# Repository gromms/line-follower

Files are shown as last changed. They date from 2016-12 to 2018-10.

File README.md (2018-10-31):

# line-follower

## Team

* Gromet Spaal
* Juhan Raedov

## Description

Goal is to develop a line follower robot that would be able to compete and
complete the track of Robotex line following with obstacles and regular line
following. The emphasis will be on line following with obstacles. 

The design will be based on [Jarek Korus'es Thunderstorm] (https://www.youtube.com/watch?v=a7_z5ovXjRw)

## Main Requirements

* Max Dimensions:  25x25x25 cm
* Max Weight: 1 kg
* Must have a start/stop button or remote
* Voltage up to 24 V

## Features

* Remote which can be used to:
 * Start and stop the line following program
 * Monitor battery voltage
 * Change PID constants
 * Control blower (on-off, speed)
 * Choose whether to use normal line following or line following with obstacles
* Sensors:
 * 14 IR light sensors for line detection
 * 2-axis accelerometer to calculate tilt angles
 * Three IR proximity sensors to detect the obstacles
 * Li-Po monitoring IC
* Arduino mini for live WiFi or bluetooth feedback of sensors (maybe include it onto main board)
 * **Reasoning:**
  - Reduces time when the main processor has to deal with things that are not related to running the main program
  - Deals with the communication with the remote
  - Can give live feedback of the sensors
   - Can be used to save the data and plot a graph of line errors

## BOM
[Google Drive spreadsheet] (https://docs.google.com/spreadsheets/d/14ZZVYrouCOKjxGVaX2KsAmJzS4HpelGW_TXLZ0HPqsI/edit#gid=0)

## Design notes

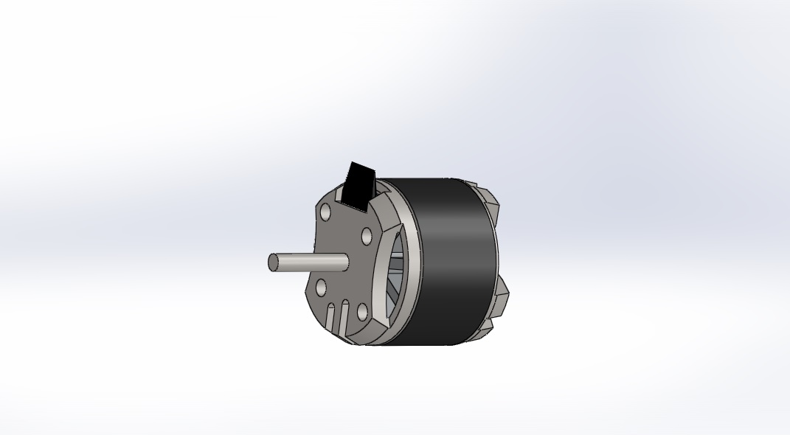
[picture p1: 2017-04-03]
SW design/Martini sumo rattad/PropDrive 28-26/Render2.jpg

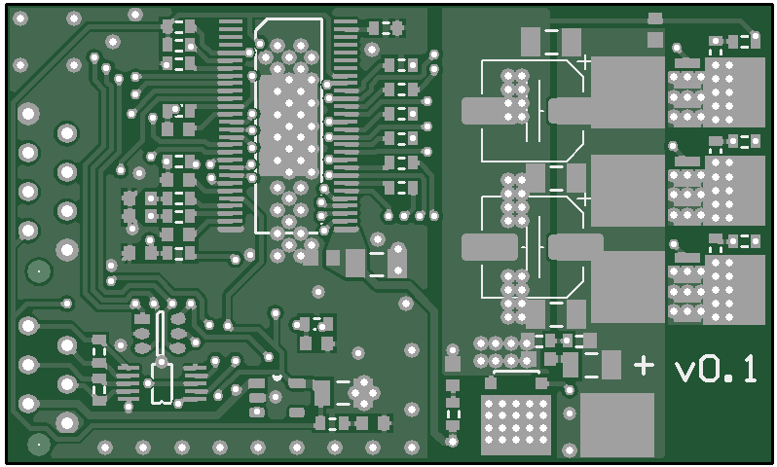
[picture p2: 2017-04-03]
SW design/bldc_driver/ibd_v01_top.png

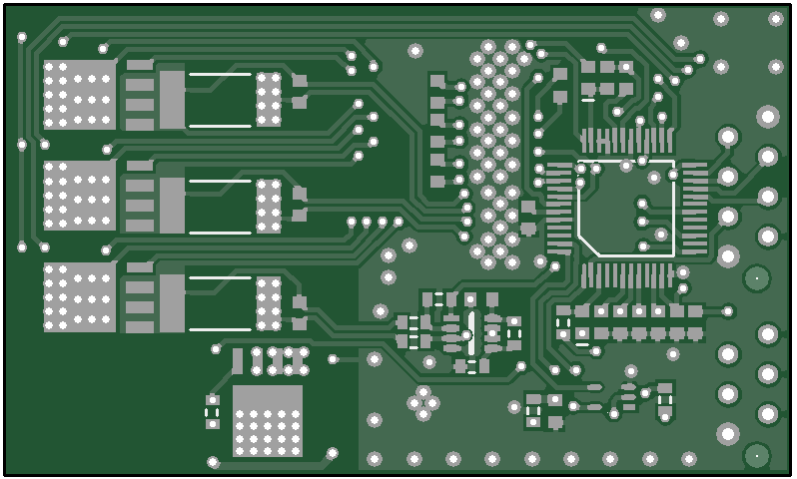
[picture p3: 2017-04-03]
SW design/bldc_driver/ibd_v01_bottom.png

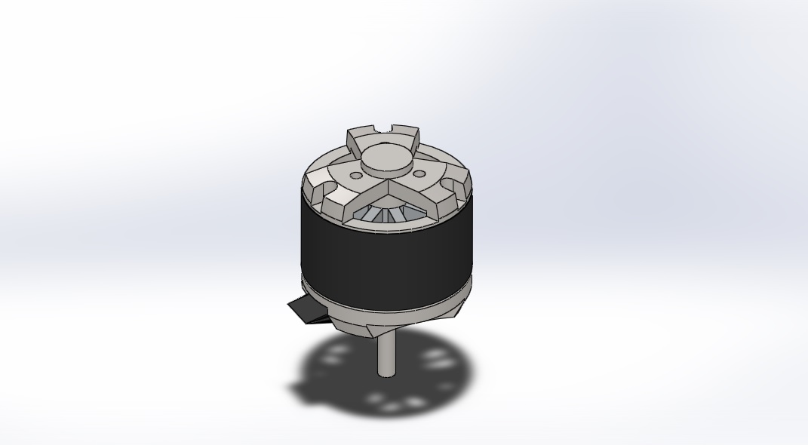
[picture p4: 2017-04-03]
SW design/Martini sumo rattad/PropDrive 28-26/Render1.jpg

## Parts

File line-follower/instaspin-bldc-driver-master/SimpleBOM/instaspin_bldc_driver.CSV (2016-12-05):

Bill of Material for
On 14.08.2016 at 22:21:20
Comment | Pattern | Quantity | Components
1.00k | J1-0603 | 2 | R32, R33 | Resistor
10.0k | J1-0603 | 3 | R34, R36, R37 | Resistor
100k | J1-0603 | 1 | R17 | Resistor
100nF | 1608[0603] | 12 | C10, C11, C12, C15, C16, C17, C18, C20, C22, C31, C32, C34 | Capacitor (Semiconductor SIM Model)
10k | J1-0603 | 4 | R26, R27, R35, R38 | Resistor
10m | 2512M | 3 | R7, R8, R9 | Resistor
10nF | 1608[0603] | 1 | C21 | Capacitor (Semiconductor SIM Model)
10R | J1-0603 | 6 | R1, R2, R3, R4, R5, R6 | Resistor
10uF | C1206 | 1 | C37 | Capacitor (Semiconductor SIM Model)
120R | J1-0603 | 2 | R44, R47 | Resistor
1k | J1-0603 | 2 | R10, R25 | Resistor
1nF | 1608[0603] | 3 | C7, C8, C9 | Capacitor (Semiconductor SIM Model)
1R | J1-0603 | 1 | R28 | Resistor
1uF | 1608[0603] | 2 | C1, C2 | Capacitor (Semiconductor SIM Model)
2.2k | J1-0603 | 2 | R24, R48 | Resistor
2.2nF | 1608[0603] | 3 | C23, C24, C25 | Capacitor (Semiconductor SIM Model)
2.2uF | 1608[0603] | 7 | C3, C26, C27, C28, C29, C30, C35 | Capacitor (Semiconductor SIM Model)
2.2uF | C1206 | 4 | C4, C5, C6, C14 | Capacitor (Semiconductor SIM Model)
220 OHM | INDC1608L | 1 | FB1 | Ferrite
220µ | CAP_ELEC_6.3x4.2 | 2 | C39, C40 | Capacitor THT Alum Elec 470uF 20% 16V
22nF | 1608[0603] | 1 | C13 | Capacitor (Semiconductor SIM Model)
25AA010 | TSOT-23-6 | 1 | U8 | EEPROM
3.3R | C1206 | 1 | R18 | Resistor
330R | J1-0603 | 1 | R42 | Resistor
34.8k | J1-0603 | 4 | R11, R12, R13, R19 | Resistor
4.7k | J1-0603 | 1 | R41 | Resistor
4.99k | J1-0603 | 4 | R14, R15, R16, R20 | Resistor
56R | J1-0603 | 3 | R21, R22, R23 | Resistor
60 OHM | INDC1608L | 1 | FB2 | Ferrite
DRV8301 | SO56_POWERPAD | 1 | U2
HEADER-1 | 2MM-BANANA-SOCKET | 5 | J16, J17, J18, J19, J26
JTAG | MICRO-MATCH-8 | 1 | J12
LED1 | 1608[0603] | 2 | D2, D3 | Typical RED GaAs LED
MOSFET-N | SOT669 | 7 | Q1, Q2, Q3, Q4, Q5, Q6, Q7
NUP4201MR6 | TSOP-6 | 1 | U3
OPA2374 | SOT23-8 | 1 | U4
RS485 | MICRO-MATCH-6 | 1 | J13
SN65HVD73 | SOP10 | 1 | U6
ZENER | SODFL370X135-2N | 1 | D1
TMS320F28027F | PQFP48 | 1 | U1

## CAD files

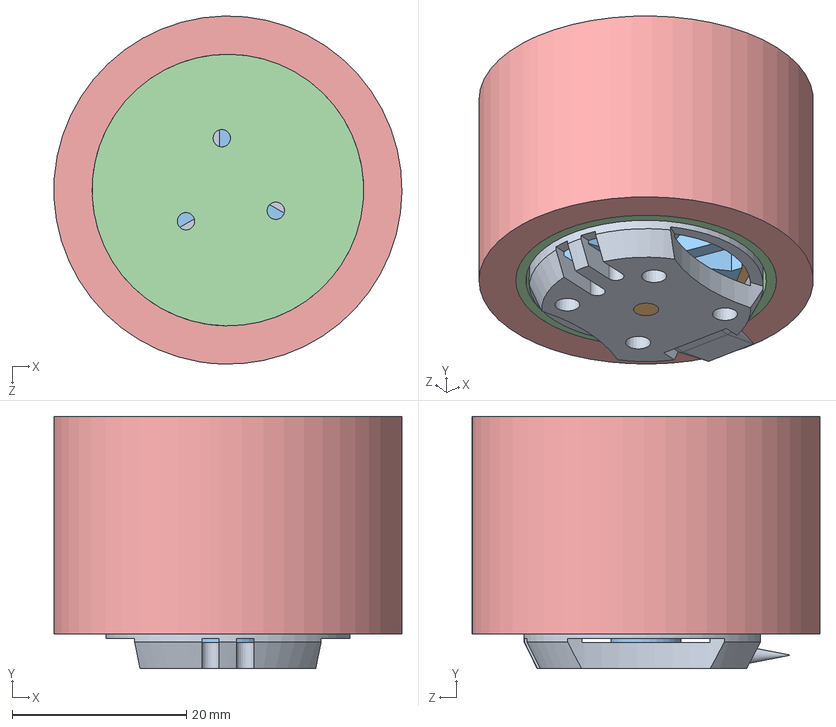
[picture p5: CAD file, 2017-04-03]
SW design/Martini sumo rattad/rehvi_raam_ja_mootor.SLDASM
40.0 x 29.0 x 40.0 mm
StatMotore
CassaMotore
InternoMotore
rehvi_raam
rehv

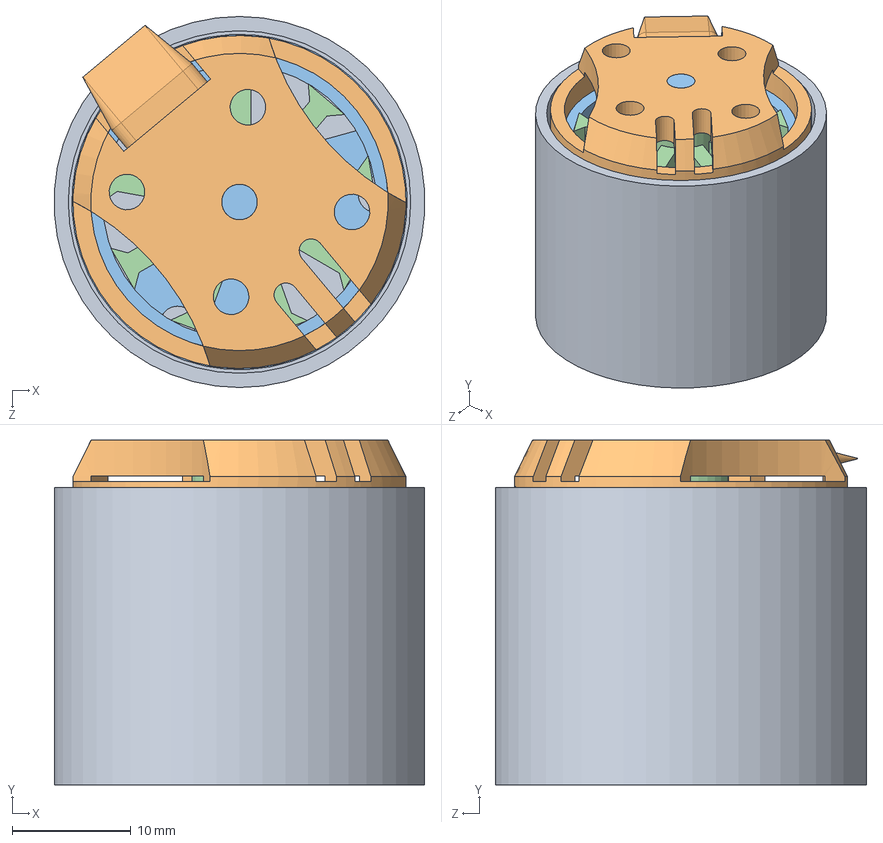
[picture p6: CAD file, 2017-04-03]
SW design/Martini sumo rattad/mootor_raamis.SLDASM
31.1 x 29.0 x 31.2 mm
rehvi_raam
StatMotore
CassaMotore
InternoMotore

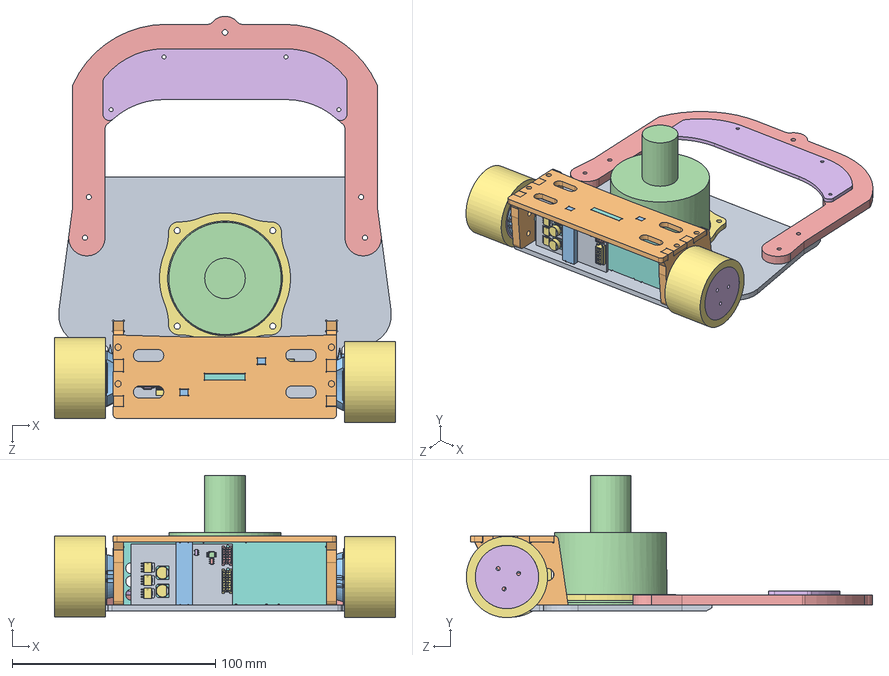
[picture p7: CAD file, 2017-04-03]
SW design/MAIN.SLDASM
167.8 x 70.0 x 199.9 mm
base
motor_mnt x 2
StatMotore x 2
CassaMotore x 2
InternoMotore x 2
rehvi_raam x 2
rehv x 2
motor_mnt_support
ibd01_Board x 2
ibd01_User_Library-sot238 x 2
ibd01_User_Library-sot353 x 2
ibd01_User_Library-msop-10 x 2
ibd01_micromatch_body_Pins6 x 2
ibd01_micromatch_pin x 12
ibd01_micromatch_body_Pins8 x 2
ibd01_micromatch_pin_2 x 16
ibd01_User_Library-LFPAK_1_1 x 14
ibd01_User_Library-LFPAK_2_1 x 14
ibd01_User_Library-LFPAK_3_1 x 14
ibd01_User_Library-LFPAK_4_1 x 14
ibd01_User_Library-LFPAK_5_1 x 14
ibd01_User_Library-LFPAK_6_1 x 14
ibd01_User_Library-LFPAK_7_1 x 14
ibd01_User_Library-LQFP48-2_case x 2
ibd01_User_Library-LQFP48-2_pin x 96
ibd01_User_Library-LQFP48-2_circle x 2
ibd01_Extruded_6 x 12
ibd01_Extruded_7 x 6
ibd01_User_Library-TSOP-6 x 2
ibd01_CircuitWorks-SOT-23-5 x 2
ibd01_Cap,_elec,_6.3x4.2 x 4
ibd01_Cap,_elec,_6.3x4.2_2 x 4
ibd01_Cap,_elec,_6.3x4.2_3 x 4
roof
ibd01_fastener x 2
edf
front5mm
front_sensors
edf_mnt

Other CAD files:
SW design/bldc_driver/ibd01_779537936.sldasm
SW design/bldc_driver/ibd01_Q6.sldasm
SW design/bldc_driver/ibd01_R8.sldasm
SW design/bldc_driver/ibd01_U3.sldasm
SW design/bldc_driver/ibd01_U4.sldasm
SW design/bldc_driver/ibd01_Q4.sldasm
SW design/bldc_driver/ibd01_U5.sldasm
SW design/bldc_driver/ibd01_R7.sldasm
SW design/bldc_driver/ibd01_J12.sldasm
SW design/bldc_driver/ibd01_micromatch_fob_6.sldasm
SW design/bldc_driver/ibd01_U1.sldasm
SW design/bldc_driver/ibd01_U7.sldasm
SW design/bldc_driver/ibd01_Q3.sldasm
SW design/bldc_driver/ibd01_C40.sldasm
SW design/bldc_driver/ibd01_User_Library-LFPAK.sldasm
SW design/2/anduriplaat.SLDPRT
SW design/2/base.SLDPRT
SW design/2/front.SLDPRT
SW design/Martini sumo rattad/PropDrive 28-26/CassaMotore.SLDPRT
SW design/Martini sumo rattad/PropDrive 28-26/InternoMotore.SLDPRT
SW design/Martini sumo rattad/PropDrive 28-26/PropDrive28-26.IGS
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

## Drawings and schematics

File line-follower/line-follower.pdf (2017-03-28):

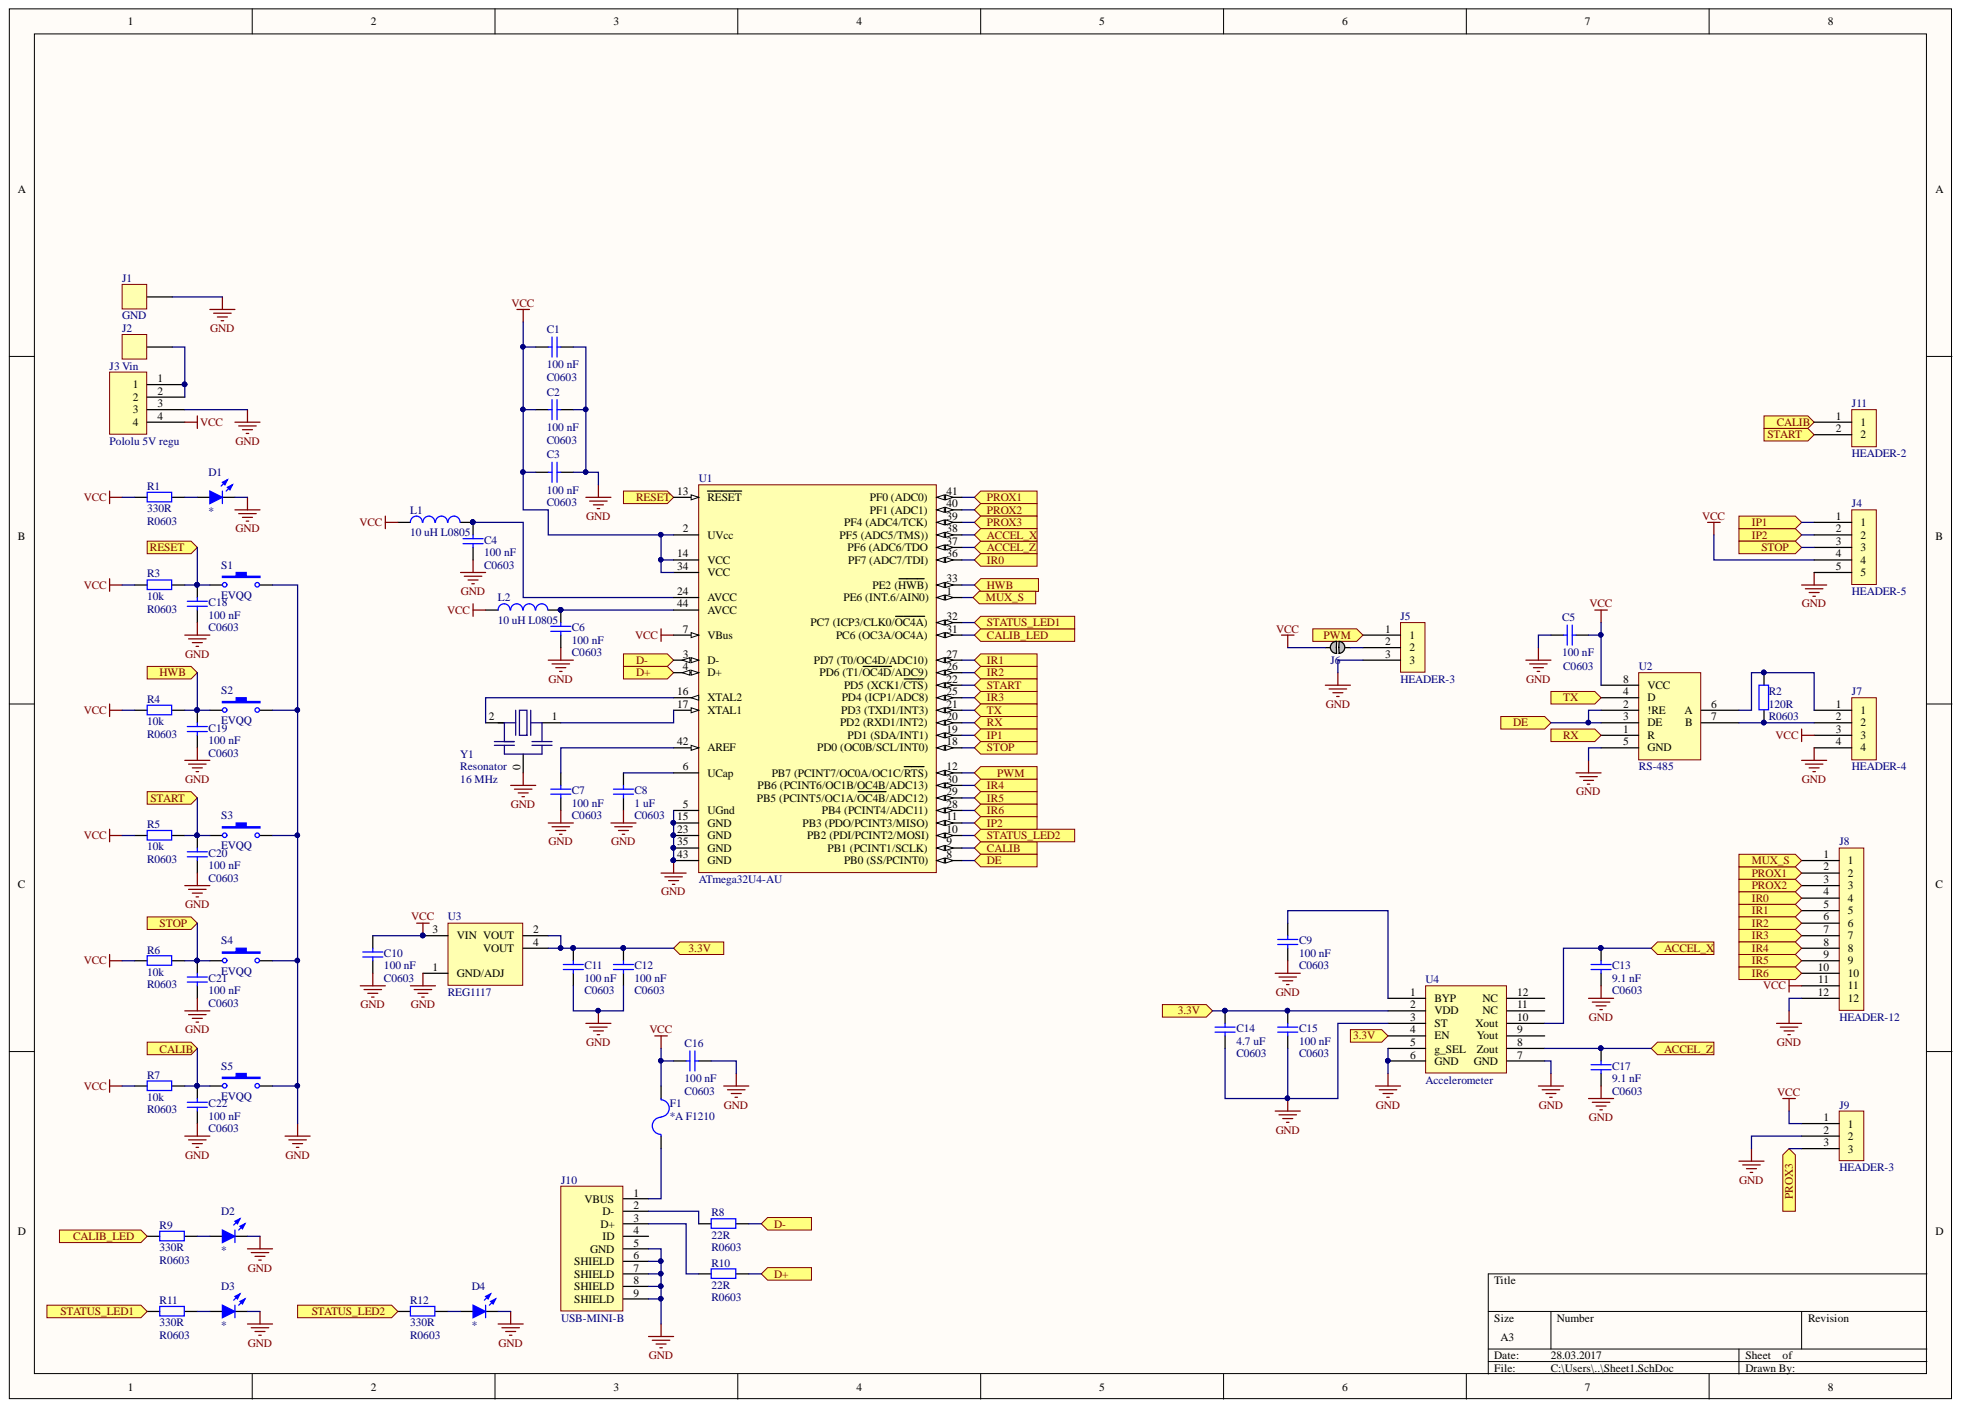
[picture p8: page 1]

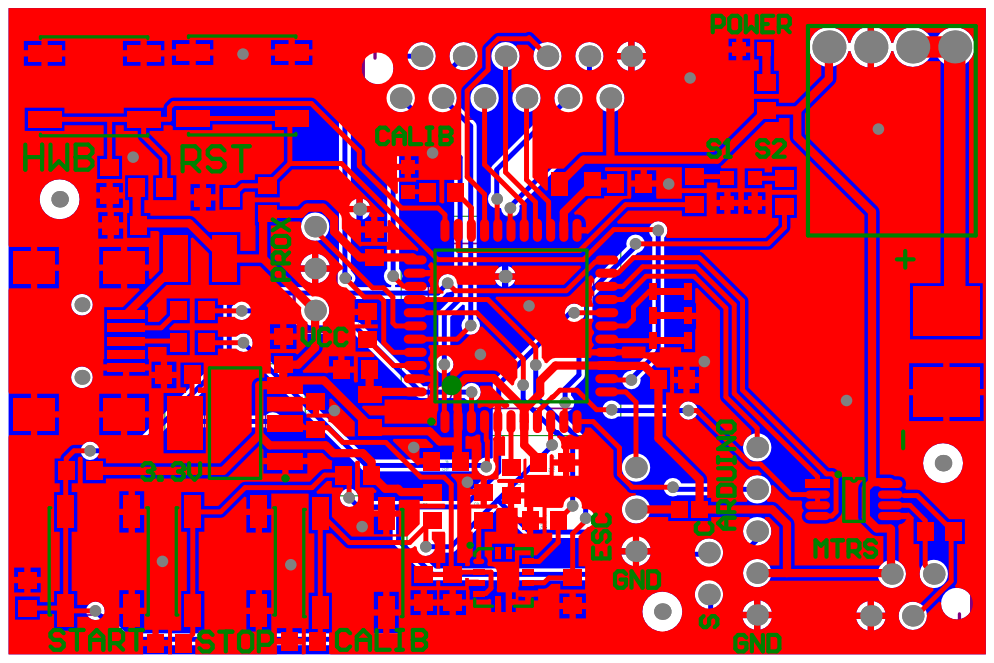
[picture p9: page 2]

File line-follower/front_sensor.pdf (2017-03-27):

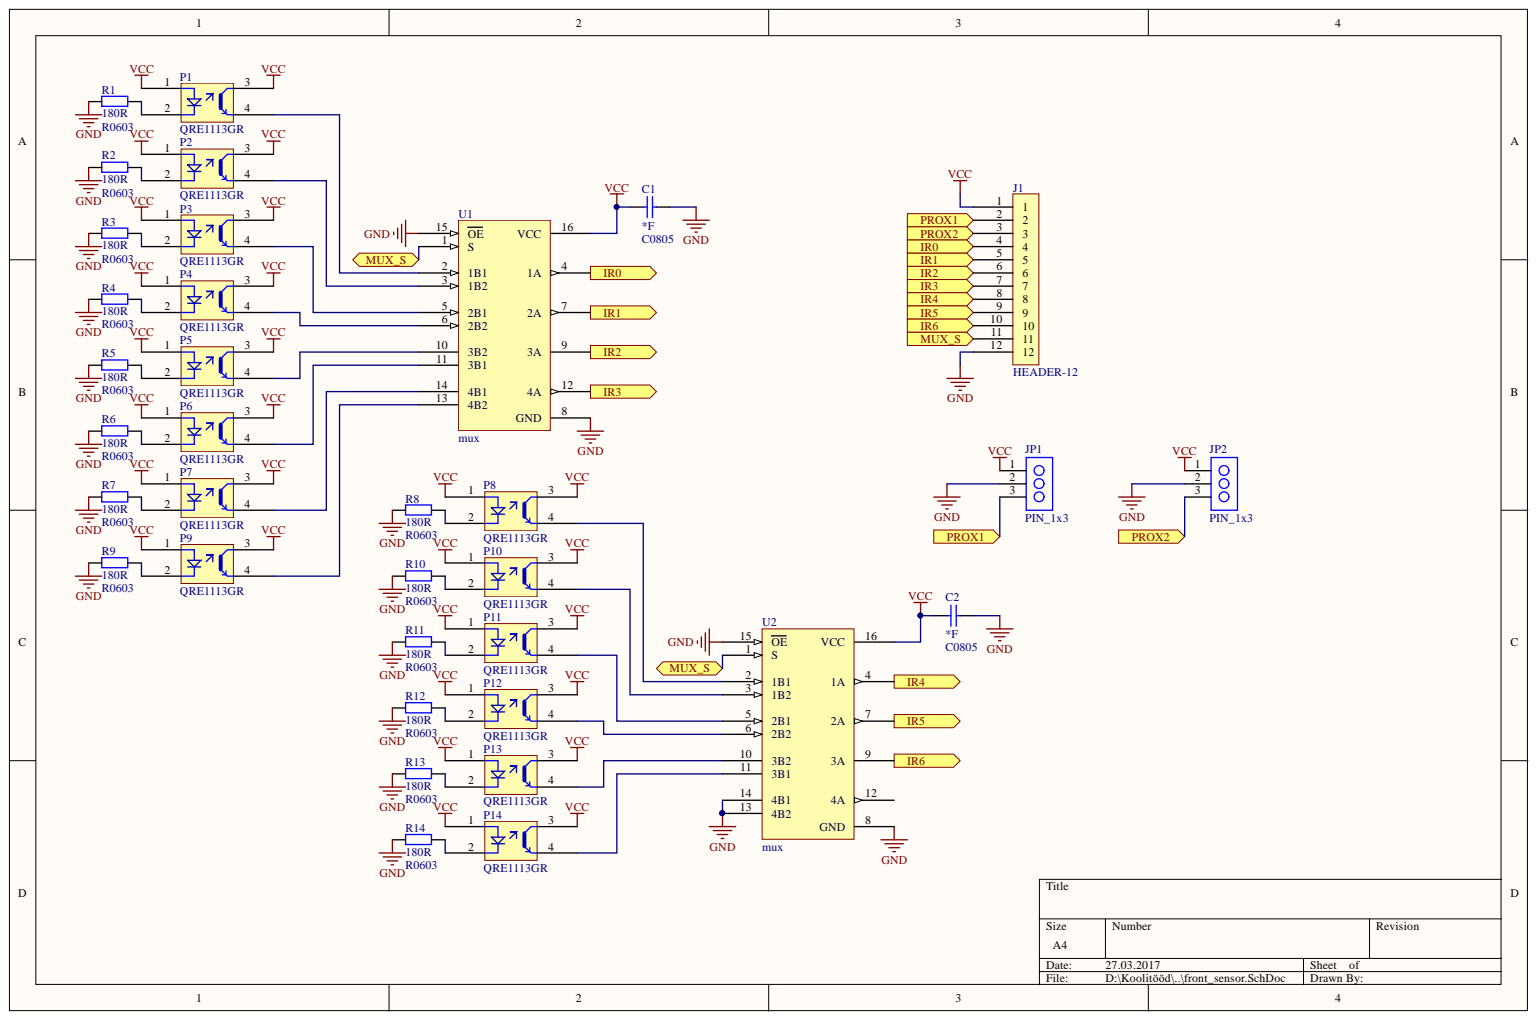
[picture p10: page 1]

MUX_S | 1B1 2

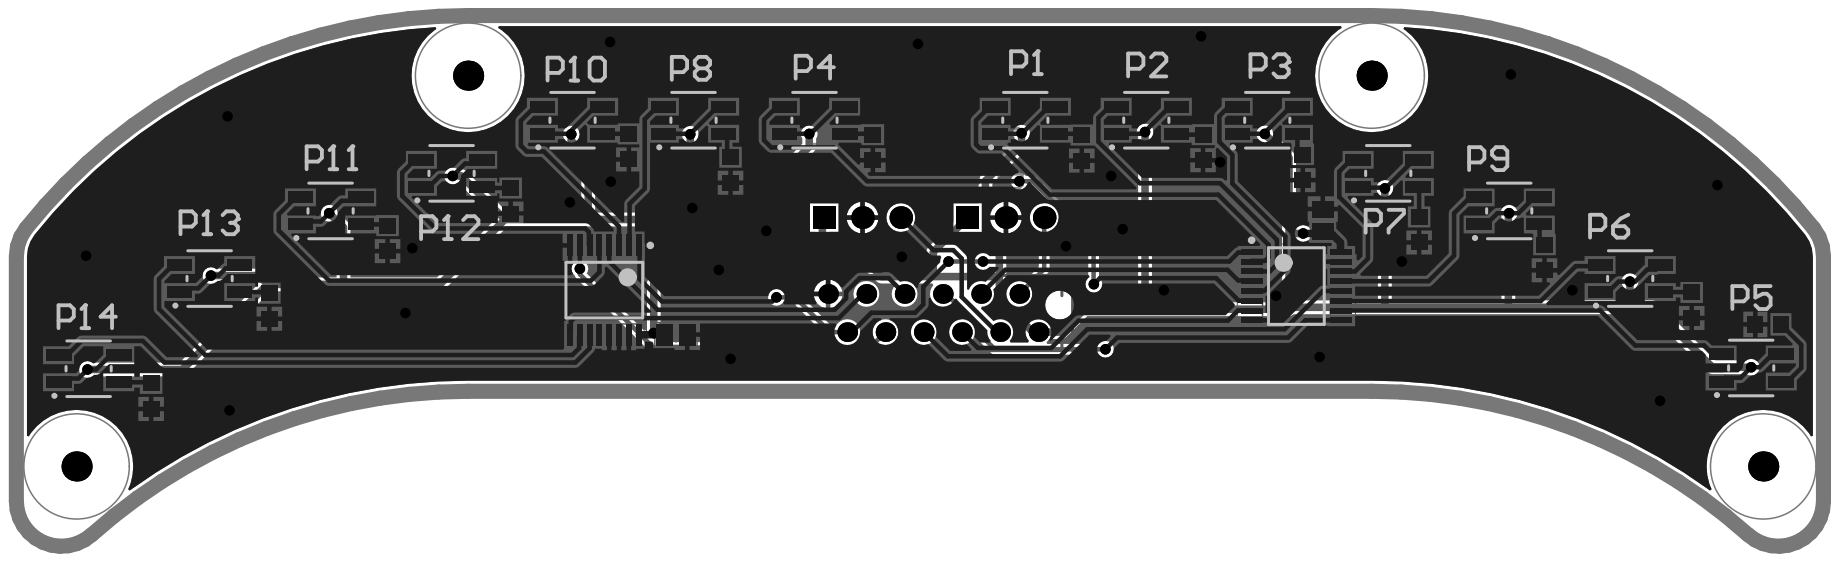
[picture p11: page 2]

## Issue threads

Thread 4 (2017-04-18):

RS-485 GND is on the wrong side

gromms, 2017-04-18:

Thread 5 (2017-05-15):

IR light sensors' transistor are connected wrongly

gromms, 2017-05-15:
Should take output from collector through 22 Ohm resistor and emitter should be connected to ground.

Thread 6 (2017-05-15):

Wrong footprint for RS-485 IC

gromms, 2017-05-15:
Distance between pads is too small. Should be 1 pad more apart.

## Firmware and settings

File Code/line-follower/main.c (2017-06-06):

#define F_CPU 16000000

#include <avr/io.h>
#include <util/delay.h>
#include <avr/interrupt.h>
#include <stdio.h>
#include <stdlib.h>

#include "pinout.h"
#include "adc.h"
#include "uart.h"
#include "esc.h"
#include "buttons.h"
#include "leds.h"
#include "usb_serial.h"
#include  "calib.h"
#include "pid.h"

uint16_t base_motor_speed = 220;
uint8_t esc_speed = 20;

bool_t esc_enabled = TRUE;

void usb_write();

void usb_write(const char *str) {
	while (*str) {
		usb_serial_putchar(*str);
		str++;
	}
}

void usb_debug()
{
	char buf[16];
	
	read_lights(light_vals);
	
	for(int i = 0; i < LIGHTS; i++)
	{
		sprintf(buf, "%d ", light_vals[i]);
		usb_write(buf);
	}
	/*
	read_proxes(prox_vals);
	for(int i = 0; i < PROXES; i++)
	{
		sprintf(buf, "%d ", prox_vals[i]);
		usb_write(buf);
	}
	printf(buf, "%d\n", adc_read(IR6));
 	
	usb_write(buf);*/
}

char buf[16];

int main(void)
{
	// Remove CLKDIV8
	CLKPR = 0x80;
	CLKPR = 0x00;
	
	// Disable JTAG
	MCUCR |= (1 << JTD);
	MCUCR |= (1 << JTD);
	
	// Set MUX_S pin as output
	DDRE = (1 << MUX_S);
	
	// Initializations
	usb_init();
	adc_init();
 	UART_init();
	if (esc_enabled)
	{
		esc_init();
	}
 	buttons_init();
	leds_init();
	calib_init(lights_max, lights_min);
	
// 	set_led(STATUS_LED1, TRUE);
// 	set_led(CALIB_LED, TRUE);
	
	sei();
	
	//_delay_ms(3000);
    
	//esc_stop();
	//motor_drive(0, 0);
	
	while(check_start_state())
	{
		set_led(STATUS_LED1, FALSE); 
		set_led(STATUS_LED2, FALSE); 
		if (detect_obtsacle(prox_vals) == 1)
			set_led(STATUS_LED2, TRUE); // wall
		else if (detect_obtsacle(prox_vals) == -1)
			set_led(STATUS_LED1, TRUE); // hill
	}
	while(calib_state())
	{
		calib_start(lights_max, lights_min);
	}
	//_delay_ms(1000);
	
	if(esc_enabled)
	{
		esc_start();
		esc_set_speed(esc_speed);
	}
	//calib_load();
	
	_delay_ms(1000);
	
	while (1) 
    {
 		
  		//read_lights(light_vals);
		
		int16_t speed = calc_speed(lights_max, lights_min);
// 		sprintf(buf, "%d \n", speed);
// 		usb_write(buf);
// 		for(int i = 0; i < LIGHTS; i++)
// 		{
// 			//sprintf(buf, "%d ", (100 * (light_vals[i] - lights_min[i])) / (lights_max[i] - lights_min[i]));
// 			sprintf(buf, "%d ",  light_vals);
// 			
// 			usb_write(buf);
// 		}
// 		usb_write("\n");
// 		read_proxes(prox_vals);
// 		for(int i = 0; i < PROXES; i++)
// 		{
// 			sprintf(buf, "%d ", prox_vals[i]);
// 			usb_write(buf);
// 		}
// 		usb_write("\n");
		
// 		int16_t error_motor_speed = Kp*get_error(light_vals, lights_min, lights_max);
// 		

// 		PORTC ^= (1 << STATUS_LED1);
// 		motor_drive(200, 200);
// 		
// 		_delay_ms(100);
// 		PORTC ^= (1 << STATUS_LED1);
// 		motor_drive(400, 400);
// 		
//  		_delay_ms(100);
// 		int16_t speed_left = speed < -100 ? -(int16_t)((double)(-speed) / 1.5) - 100 : base_motor_speed + speed;
// 		int16_t speed_right = speed > 100 ? -100 - (int16_t)((double)speed / 1.5)  : base_motor_speed - speed; 
		int16_t speed_left = base_motor_speed + speed;
		int16_t speed_right = base_motor_speed - speed;
 		motor_drive(speed_left, speed_right);
		//motor_drive(0, 0);
// 		
// 		sprintf(buf, " -- %d", error_motor_speed);
// 		usb_write(buf);
// 
// 		usb_write("\n");

// 		for(int i = 0; i < 800; i++)
// 		{
// 			motor_drive(i, i);
// 			_delay_ms(10);
// 		}
// 		for(int i = 800; i > 0; i--)
// 		{
// 			motor_drive(i, i);
// 			_delay_ms(10);
// 		}
// 	    
 	}
}

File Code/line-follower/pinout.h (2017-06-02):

#ifndef PINOUT_H
#define PINOUT_H

#include <avr/io.h>

#define TRUE 1
#define FALSE 0
typedef unsigned char bool_t;

#define CLEAR_PIN(port, pin) (port &= ~(1 << pin))
//#define BIT_SET(a,b) ((a) = (1<<(b)))
#define CHECK_PIN(port, pin) (port & (1 << pin))

void BIT_SET(uint8_t *port, uint8_t pin);

// Proximity sensors

#define PROX1 0b000000
#define PROX2 0b000001
#define PROX3 0b000100


// Accelerometer 

#define ACCEL_X 0b000101	
#define ACCEL_Z 0b000110


// IR line sensors

#define IR0 0b000111
#define IR1 0b100010
#define IR2 0b100001
#define IR3 0b100000
#define IR4 0b100101
#define IR5 0b100100
#define IR6 0b100011


// Line sensors' multiplexer select

#define MUX_S PE6


// Arduino interrupt pins

#define IP1 INT1
#define IP2 PCINT2


// LEDs

#define STATUS_LED1 PC7
#define STATUS_LED2 PB2
#define CALIB_LED PC6


// Buttons

#define START PD5
#define STOP INT0
#define CALIB PB1


// RS-485 pins

#define DE PB0
#define RX RXD1
#define TX TXD1


// ESC PWM pin

#define ESC_PWM PB7

void write_pins(uint16_t, uint16_t);
void read_pin(uint16_t, uint16_t);

#define LIGHTS_PER_HALF 7
#define LIGHTS 14
#define PROXES 3

uint16_t light_vals[LIGHTS];
uint16_t prox_vals[PROXES];

uint16_t lights_max[LIGHTS];
uint16_t lights_min[LIGHTS];

#endif

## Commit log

2016-12-05 Initial commit with /ReikoR's instaspin driver
    [BOOSTXL-DRV8301.PcbLib, BOOSTXL-DRV8301.SCHLIB, Sheet1.SchDoc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]
2016-12-06 Get started with electronics design
    [Sheet1.SchDoc, line-follower.PrjPcb]
2017-03-07 Make SW drawings v2
    [ASSM.SLDASM, MAIN.SLDASM, alu_edf.SLDPRT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]
2017-03-07 add bom to readme file
2017-03-12 update SW desing - engines+engine controllers
    [ASSM.SLDASM, CassaMotore.SLDPRT, InternoMotore.SLDPRT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]
2017-03-12 add spoiler/roof to SW design
    [MAIN.SLDASM, motor_mnt.SLDPRT, roof.SLDPRT]
2017-03-13 Start working on electronics
    [PcbLib1.PcbLib, Schlib1.SchLib, Sheet1.SchDoc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]
2017-03-14 Update resonator symbol
    [Schlib1.SchLib]
2017-03-14 Add necessary components to run the Atmega
    [Sheet1.SchDoc, line-follower.PrjPcb]
2017-03-19 tune SW design (update dimensions, hopefully solve some strength issues)
    [MAIN.SLDASM, PropDrive28-26.SLDASM, alu_edf.SLDPRT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]
2017-03-20 Finish main board schematic
    [PcbLib1.PcbLib, Schlib1.SchLib, Sheet1.SchDoc]
2017-03-20 Replace atmega schematic with one that has footprint and 3D model
    [Sheet1.SchDoc]
2017-03-21 front sensor board initial commit
    [PcbLib1.PcbLib, Schlib1.SchLib, connectors.SchLib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]
2017-03-22 finish front sensor pcb v1
    [front_sensor.PcbDoc, front_sensor.SchDoc]
2017-03-22 move connectors to correct side of the pcb
    [front_sensor.PcbDoc]
2017-03-26 improve front sensor pcb layout. Run DRC - weird error with some micromatch pins
    [front_sensor.PcbDoc, front_sensor.PrjPCB]
2017-03-27 make micromatch pins 9-12 plated
    [front_sensor.PcbDoc]
2017-03-27 Finish first version of main board design
    [Schlib1.SchLib, Sheet1.SchDoc, line-follower.PrjPcb]
2017-03-27 Add thermal relief to main board polygon
    [Sheet1.SchDoc, line-follower.PrjPcb]
2017-03-27 Add PCB design file
    [main_board.PcbDoc]
2017-03-27 fix gre1113 silk screen. update front sensor plate
    [PcbLib1.PcbLib, Schlib1.SchLib, front_sensor.PcbDoc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]
2017-03-27 add pdf of front sensor plate
2017-03-28 Add capacitors to buttons and LDO
    [Sheet1.SchDoc, main_board.PcbDoc]
2017-03-28 Add arduino pins to buttons; closes #3
    [Sheet1.SchDoc, main_board.PcbDoc]
2017-03-28 Fix port directions
    [Sheet1.SchDoc]
2017-03-28 Swap RS-485 module RX and TX
    [Sheet1.SchDoc, main_board.PcbDoc]
2017-03-28 Repour polygons
    [main_board.PcbDoc]
2017-04-03 Add board shape to keep-out layer
    [main_board.PcbDoc]
2017-04-03 Add Gerber files
    [line-follower.PrjPcb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]
2017-05-03 Add initializers for ADC, UART, LEDS and buttons.
2017-05-03 Replace stop button value with defined value
    [buttons.c, pinout.h]
2017-05-15 Add core functionality of buttons, motor controls and leds
2017-05-29 Add prescaler for ADC
2017-05-29 add basic motor control and pid
2017-05-29 add fix to basic motor speed ctrl
    [main.c]
2017-05-29 fix2 basic motor speed ctrl
    [main.c]
2017-06-02 add PD functionality for motor controlling
2017-06-05 fix pid error calc
2017-06-05 Tune PID parameters
